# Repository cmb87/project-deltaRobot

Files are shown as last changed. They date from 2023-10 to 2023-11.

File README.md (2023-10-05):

# Nema17 Delta Robot (WIP!)

Parametric Delta Robot with NEMA17 stepper motors. By selecting the length of the profiles (e,f,rf,re) the desired workspace and characteristics can be achieved.

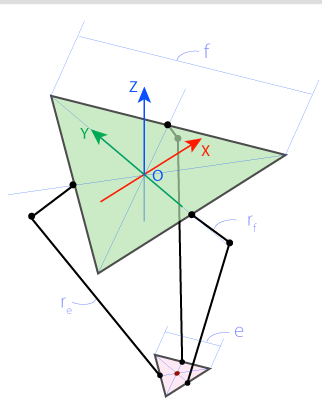
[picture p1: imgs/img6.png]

*Geometric parameters, sketch taken from https://hypertriangle.com/~alex/delta-robot-tutorial/*

# Software

For forward and inverse kinematics please check this awesome source: https://hypertriangle.com/~alex/delta-robot-tutorial/

# Construction

See https://www.thingiverse.com/thing:6248772

Pulley is a remix from here: https://www.thingiverse.com/thing:16627

## Electronics

CNC Shield: https://github.com/Protoneer/Fritzing_Parts

## To buy

    6x Senkkopfschrauben Edelstahl A2 V2A DIN 7991 Innensechskant M8 8 x 40 mm
    12x Gelenkkopf Außen M8  Uniballgelenk Kugelkopf Links und Rechts
    3x 6mm GT2 Zahnrad Pulley Ritzel Scheibe 40Zahn Ø8mm
    3x Nema17 Planetengetriebe Gear Reducer Ratio 5:1 φ5mm Input Shaft
    3x GT2 6mm geschloßener Zahnriemen 256
    6x Kugellager 61906 2RS Kugellager 6906 2RS 30x47x9mm
    3x M8 Gewindestange 10cm
    6x M8 Mutter
    3x Aluprofile (L5,) 20x20mm

    6x Aluprofile (L1 == f) 20x20mm
    3x Aluprofile (L2 == rf) 20x20mm
    3x Aluporfile (L3 == e) 10x10mm
    6x GFK/Aluminium Rundrohr 10cm  (L4==re) Durchmesser

    1x CNC Shield V3 Development Board for A4988 drivers Stepper for 3D printer compatible with Arduino
    1x Arduino Mega
    3x Micro Limit Switch
    3x Nema17 Stepper Motor

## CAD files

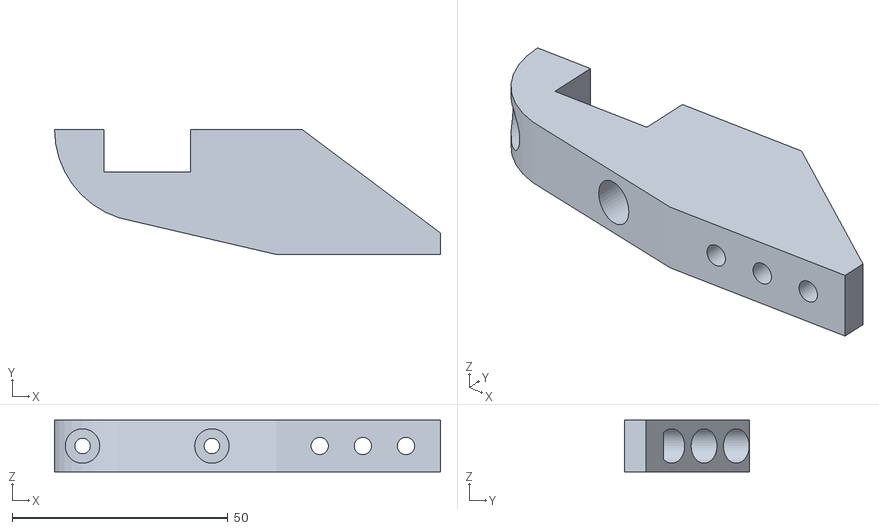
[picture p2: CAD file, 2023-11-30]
construction/3dprinted/plattformHolderUp.stl
89.5 x 29.0 x 12.0

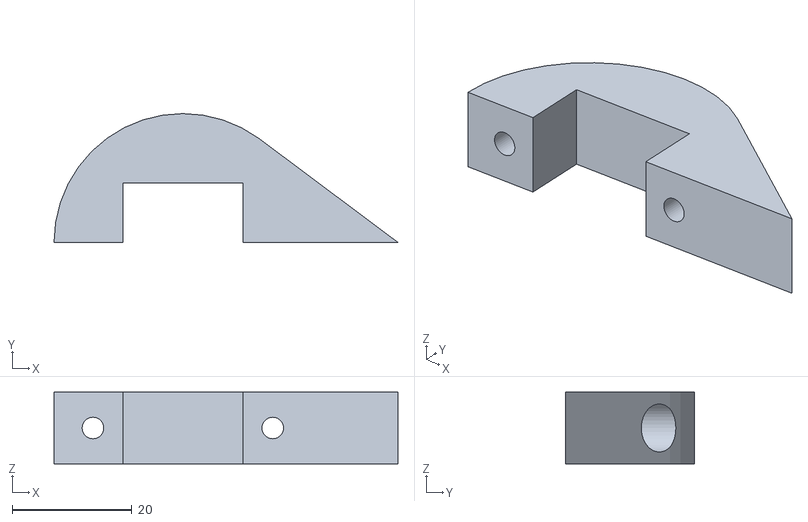
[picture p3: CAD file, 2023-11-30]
construction/3dprinted/plattformHolderLow.stl
57.4 x 21.5 x 12.0

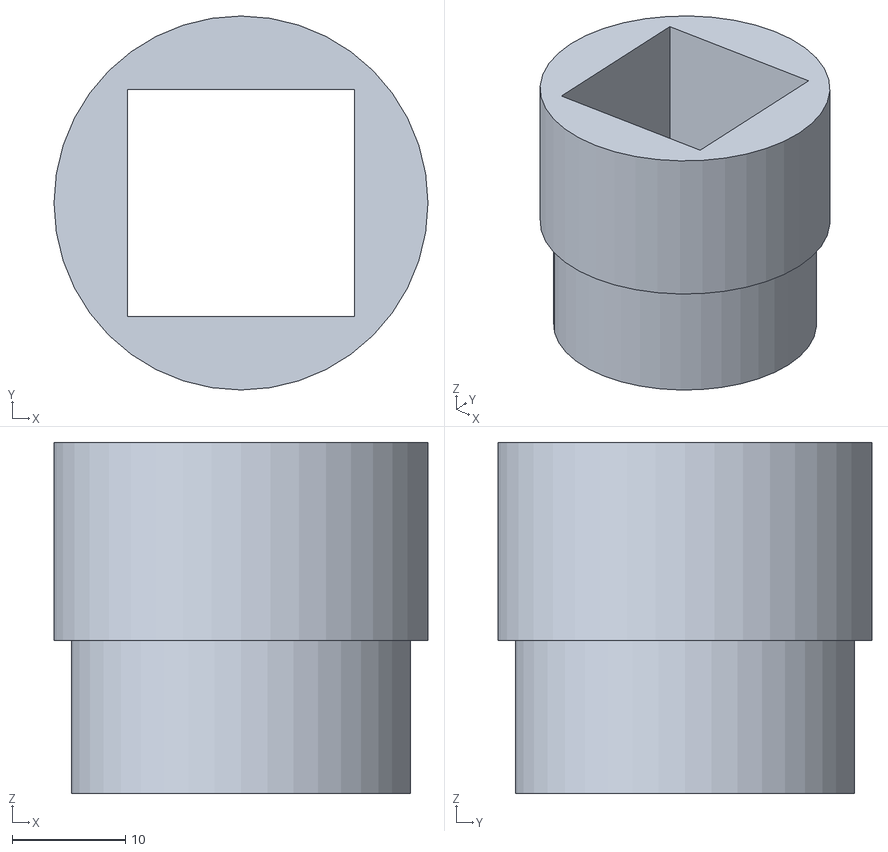
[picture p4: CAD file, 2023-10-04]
construction/3dprinted/attachment3.stl
33.0 x 33.0 x 31.0

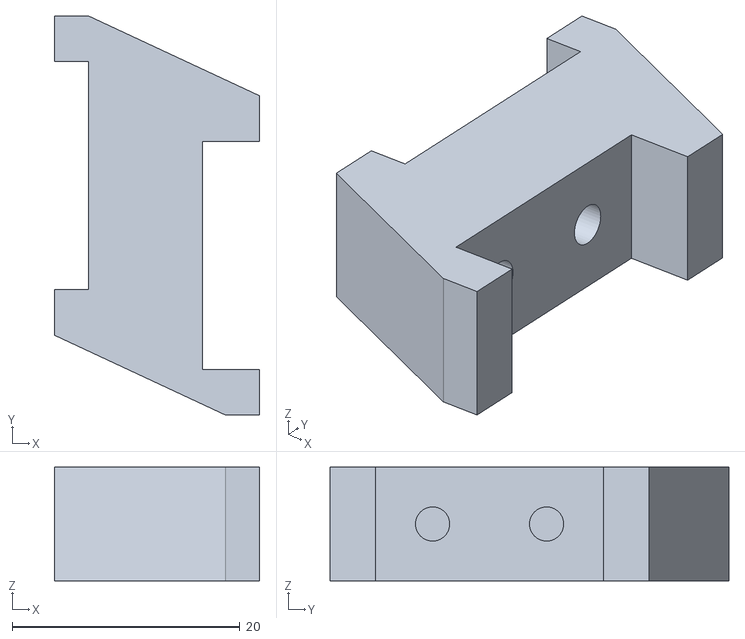
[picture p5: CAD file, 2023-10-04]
construction/3dprinted/arm_sensor_dist_v2.stl
18.0 x 35.0 x 10.0

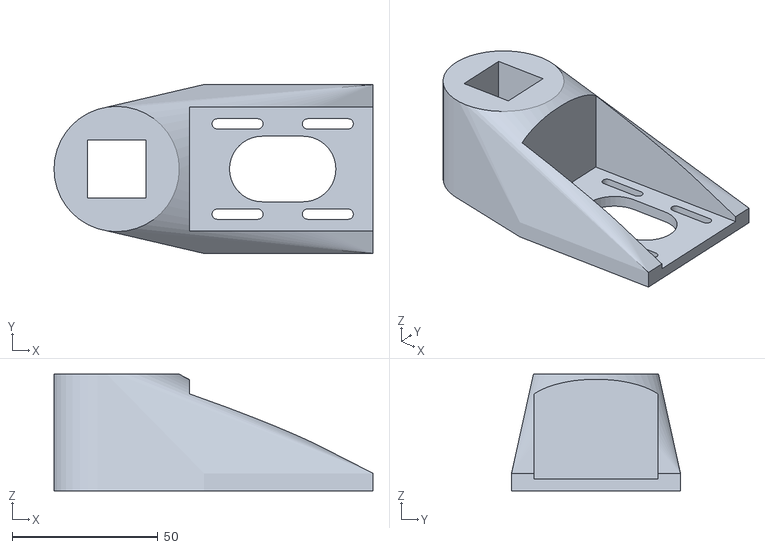
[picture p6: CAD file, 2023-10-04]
construction/3dprinted/motorHolder.stl
109.5 x 58.0 x 40.0

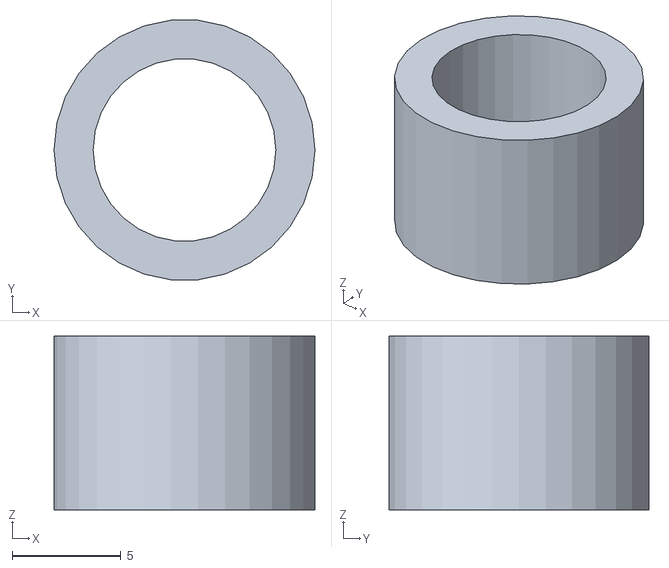
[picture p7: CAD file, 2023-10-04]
construction/3dprinted/distanceHullshort.stl
12.0 x 11.9 x 8.00

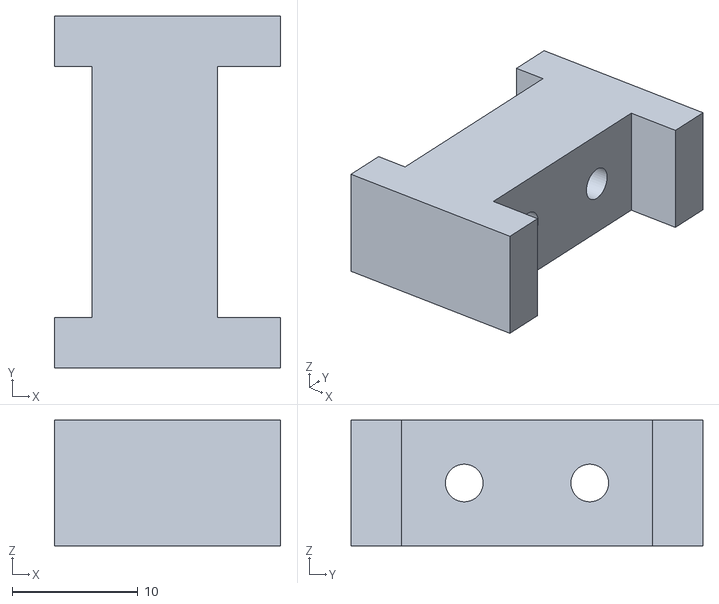
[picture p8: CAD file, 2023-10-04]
construction/3dprinted/arm_sensor_dist.stl
18.0 x 28.0 x 10.0

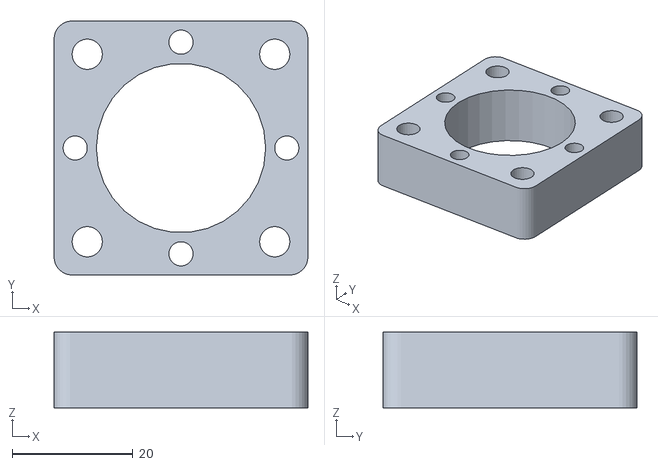
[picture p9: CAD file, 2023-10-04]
construction/3dprinted/gearadapter.stl
42.0 x 42.0 x 12.5

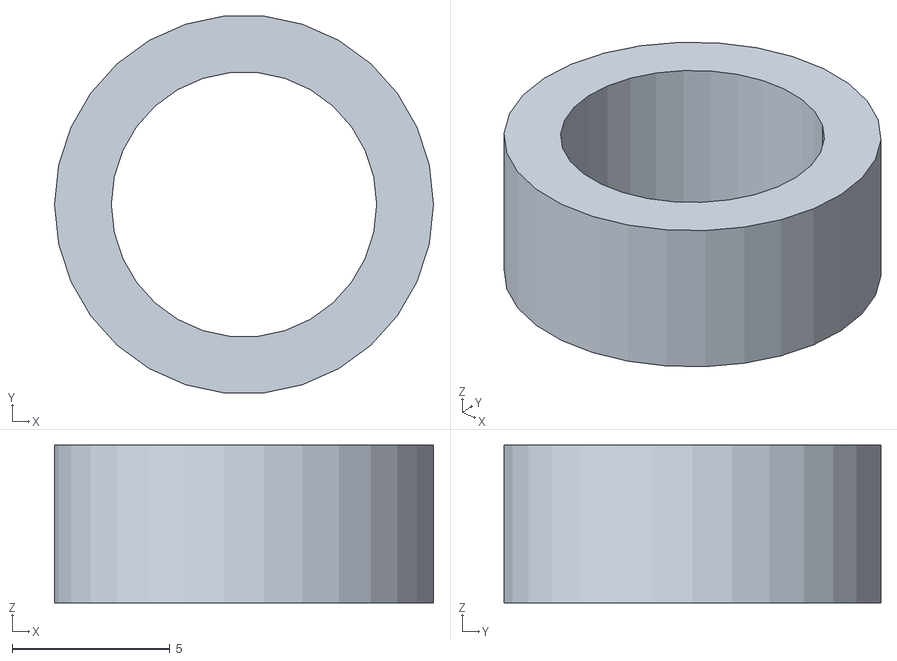
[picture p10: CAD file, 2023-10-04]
construction/3dprinted/distanceHullSupershort.stl
12.0 x 11.9 x 5.00

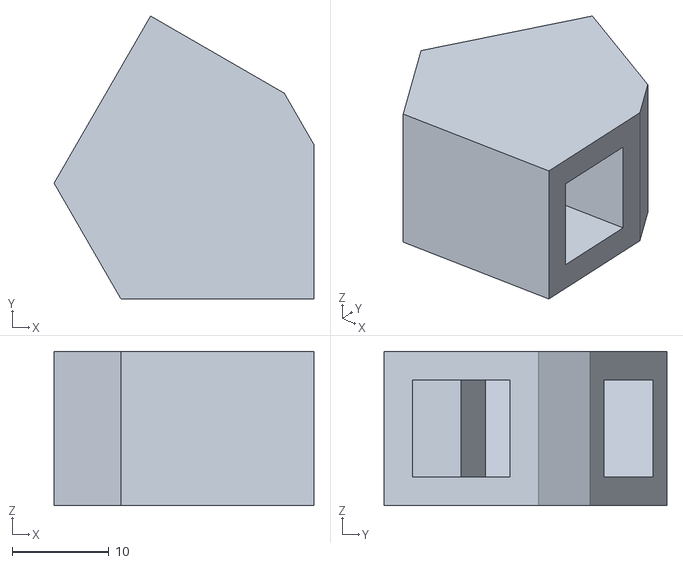
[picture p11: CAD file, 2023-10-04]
construction/3dprinted/lowerCorner.stl
26.9 x 29.3 x 16.0

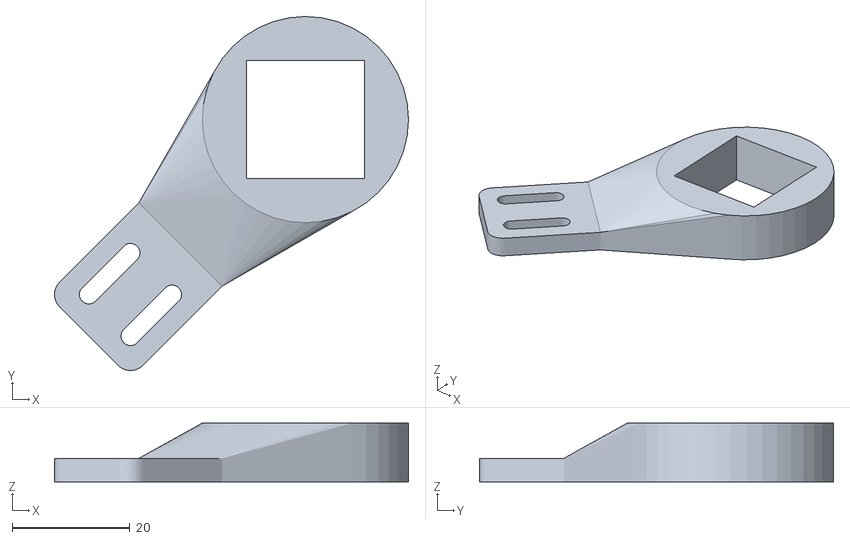
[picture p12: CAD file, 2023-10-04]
construction/3dprinted/arm_sensor_v2.stl
60.1 x 60.1 x 10.0

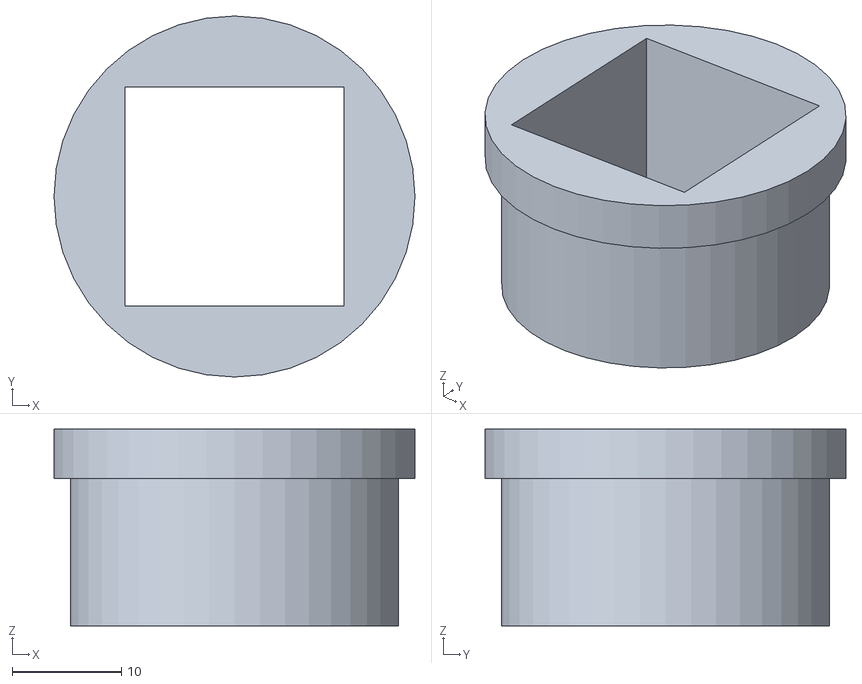
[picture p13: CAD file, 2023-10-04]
construction/3dprinted/attachment2.stl
33.0 x 33.0 x 18.0

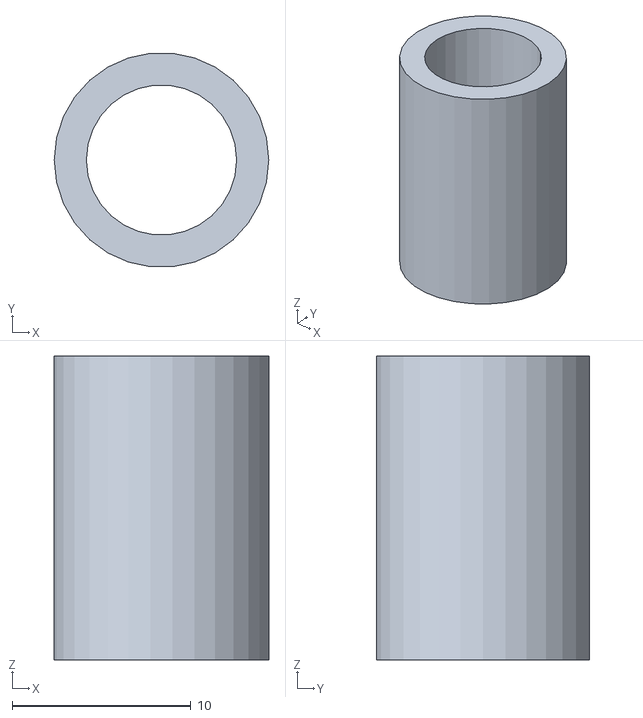
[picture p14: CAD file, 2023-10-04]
construction/3dprinted/distanceHull.stl
12.0 x 11.9 x 17.0

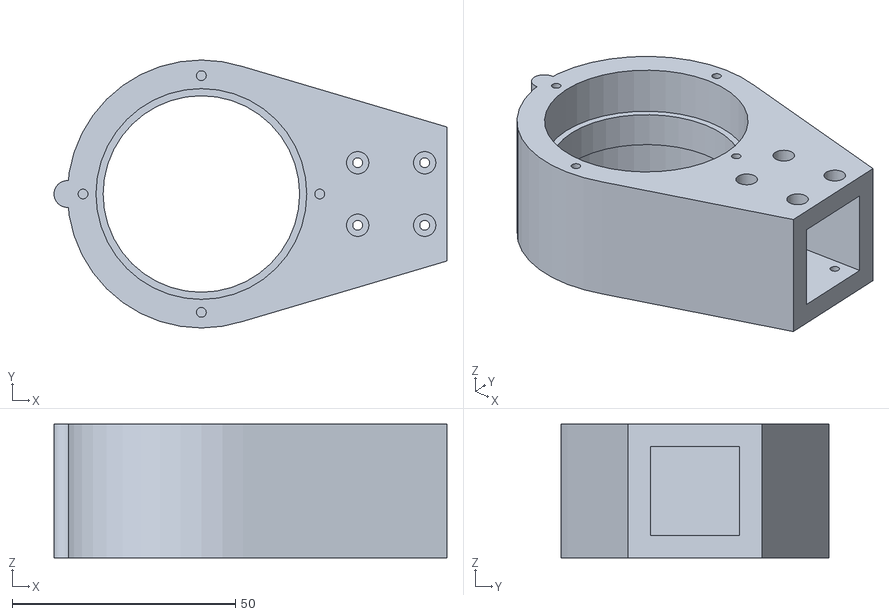
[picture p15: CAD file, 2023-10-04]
construction/3dprinted/arm.stl
88.0 x 60.0 x 30.0

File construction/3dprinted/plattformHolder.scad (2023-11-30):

//translate([50,0,+20])rotate([0,180,0])color("red")import("motor_nema17.stl");

difference(){
hull(){
translate([0,0,0])cylinder(r=43/2, h=12, $fn=40);
translate([30,-58/2,0])cube([38,5,12]);
}
translate([-20.0/2,-19.8/2,-1])cube([20.0,19.8,72]);  

translate([50,+70/2,6])rotate([90,0,0])cylinder(r=2, h=70, $fn=40);
translate([60,+70/2,6])rotate([90,0,0])cylinder(r=2, h=70, $fn=40);
translate([40,+70/2,6])rotate([90,0,0])cylinder(r=2, h=70, $fn=40);

translate([50,+70/2+15,6])rotate([90,0,0])cylinder(r=4, h=70, $fn=40);
translate([60,+70/2+15,6])rotate([90,0,0])cylinder(r=4, h=70, $fn=40);
translate([40,+70/2+15,6])rotate([90,0,0])cylinder(r=4, h=70, $fn=40);

translate([15,+70/2,6])rotate([90,0,0])cylinder(r=1.8, h=70, $fn=40);
translate([-15,+70/2,6])rotate([90,0,0])cylinder(r=1.8, h=70, $fn=40);

translate([-15,-5,6])rotate([90,0,0])cylinder(r=4, h=70, $fn=40);
translate([-15,70+5,6])rotate([90,0,0])cylinder(r=4, h=70, $fn=40);

translate([15,-5,6])rotate([90,0,0])cylinder(r=4, h=70, $fn=40);
translate([15,70+5,6])rotate([90,0,0])cylinder(r=4, h=70, $fn=40);


//translate([-30,0,-2])cube([120,100,42]); // Comment for low
translate([-30,-100,-2])cube([120,100,42]); // Comment for up

}

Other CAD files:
construction/3dprinted/arm_tip.stl
construction/3dprinted/lowerJoint.stl
construction/3dprinted/connector.stl
construction/3dprinted/arm_pulley.stl
construction/3dprinted/arm.scad
construction/3dprinted/arm_pulley.scad
construction/3dprinted/arm_sensor.scad
construction/3dprinted/arm_sensor_dist.scad
construction/3dprinted/arm_tip.scad
construction/3dprinted/arm_uppley.scad
construction/3dprinted/attachment2.scad
construction/3dprinted/attachment3.scad
construction/3dprinted/connector.scad
construction/3dprinted/corner.scad
construction/3dprinted/corner.stl
construction/3dprinted/gearadapter.scad
construction/3dprinted/lowerCorner.scad
construction/3dprinted/lowerJoint.scad
construction/3dprinted/motorHolder.scad

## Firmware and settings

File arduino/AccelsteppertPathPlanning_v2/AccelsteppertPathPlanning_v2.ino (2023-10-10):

#include <AccelStepper.h>
#include <MultiStepper.h>
#include "SerialTransfer.h"
#include "DeltaKinematics.h"


// Pin Definitions
#define stepPinX 2 //X.STEP
#define dirPinX 5 // X.DIR

#define stepPinY 3 //Y.STEP
#define dirPinY 6 // Y.DIR

#define stepPinZ 4 //Z.STEP
#define dirPinZ 7 // Z.DIR
  
#define enablePin 8


// On the CNC shield the limit switches are expected to be normally open and 
// are wired to ground with the internal pullup enabled. The switch will read high 
// when not actuated (open) and low when actuated (closed).
// Both switches for each axis go to one pin. X+ and X- go to pin 9, Y+ and Y- to 10, Z+ and Z- to 11.
#define limitPinX 9 
#define limitPinY 10
#define limitPinZ 11


// Delta Definitions
#define Multiplier 6.583333333333333 //2370.0/360  = 95.0/40.0 * 5.0/1.0 * 200/360 = 11.875 * 200/360 
#define HomeAngle 40 //11 degrees from vertical or 79 degrees from horizontal
#define Speed 2000
#define Acceleration 3000.0


// Create MultiStepper instance
AccelStepper Xaxis(1, stepPinX, dirPinX); // pin 2 = step, pin 5 = direction
AccelStepper Yaxis(1, stepPinY, dirPinY); // pin 2 = step, pin 5 = direction
AccelStepper Zaxis(1, stepPinZ, dirPinZ); // pin 2 = step, pin 5 = direction
DeltaKinematics DK(0.18,0.384,0.04,0.15);

MultiStepper steppers;  

// For serial transfer
SerialTransfer myTransfer;

struct __attribute__((packed)) CONTROLL {
  long theta1;
  long theta2;
  long theta3;
  long enabled;
  long home;
} controllStruct;

struct __attribute__((packed)) STATE {
  float theta1;
  float theta2;
  float theta3;
  long enabled;
  long home;
  long status;
} stateStruct;

struct __attribute__((packed)) POSITION {
  float x;
  float y;
  float z;
} positionStruct;


float P0[3] = {0, 0, 0};      // Initial positions  
float Pf[3] = {0, 0, 0};      // Final positions  
float V0[3] = {0, 0, 0};      // Initial velocities  
float Vf[3] = {0, 0, 0};      // Final velocities  
float T = 0.5;              // Total time (seconds)  
float dt = 0.0005;          // Time step (seconds)  


// ==================================
float cubicPath(float t, float P0, float Pf, float V0, float Vf, float T) {  
  float a0 = P0;  
  float a1 = V0;  
  float a2 = (3 * (Pf - P0) - (2 * V0 + Vf) * T) / (T * T);  
  float a3 = (2 * (P0 - Pf) + (V0 + Vf) * T) / (T * T * T);  
  
  float position = a0 + a1 * t + a2 * t * t + a3 * t * t * t;  
  return position;  
} 

// ==================================
void Enabled(){ digitalWrite(enablePin,LOW);}

// ==================================
void Disabled(){digitalWrite(enablePin,HIGH);}

// ==================================
void sendController(float theta1, float theta2, float theta3, long home, long status){
  /**
  Function which sends state back to controller (python script) via serial protocol.
  */

  stateStruct.theta1 = theta1;
  stateStruct.theta2 = theta2;
  stateStruct.theta3 = theta3;

  stateStruct.enabled = 1;
  stateStruct.home = home;
  stateStruct.status = status;

  uint16_t sendSize = 0;
  sendSize = myTransfer.txObj(stateStruct, sendSize);
  myTransfer.sendData(sendSize);

}

// ==================================
void homeMachine(){
  /**
  Function for homing machine
  */

  // Let controller know we are homing, all since we are not homed yet (=0), all angles are unkown (-1) and busy (503)
  sendController(-1, -1, -1, 0, 503);

  // Set speed for homing
  Xaxis.setSpeed(300); 
  Yaxis.setSpeed(300); 
  Zaxis.setSpeed(300); 

  // Important assumption: all arms are lower than HomeAngle!!!! Otherwise we crash :X
  while(digitalRead(limitPinX) == HIGH || digitalRead(limitPinY) == HIGH || digitalRead(limitPinZ) == HIGH)
  {
    if(digitalRead(limitPinX) == HIGH){
      Xaxis.runSpeed();
    } else {
      Xaxis.stop();
    }
    if(digitalRead(limitPinY) == HIGH){
      Yaxis.runSpeed();
    } else {
      Yaxis.stop();
    }
    if(digitalRead(limitPinZ) == HIGH){
      Zaxis.runSpeed();
    } else {
      Zaxis.stop();
    }  
  }
  
  // Store current steps
  Xaxis.setCurrentPosition((90-HomeAngle)*Multiplier);
  Yaxis.setCurrentPosition((90-HomeAngle)*Multiplier);
  Zaxis.setCurrentPosition((90-HomeAngle)*Multiplier);

  // Let controller know we are homed and ready for receiving orders
  sendController(
    90-HomeAngle*Multiplier,
    90-HomeAngle*Multiplier,
    90-HomeAngle*Multiplier,
    1,
    200
  );

}

// ==================================
void SetMotors(){  
  Serial.print("Error"); 
  Serial.println(DK.inverse()); // cal inverse Delta Kinematics
  double A = DK.a*Multiplier;
  double B = DK.b*Multiplier;
  double C = DK.c*Multiplier;
  Serial.println(DK.a);
  Serial.println(DK.b);
  Serial.println(DK.c);
  Serial.println(DK.x);
  Serial.println(DK.y);
  Serial.println(DK.z);
  Serial.println();
  Xaxis.moveTo(A);
  Yaxis.moveTo(B);
  Zaxis.moveTo(C);
  
  while(Xaxis.distanceToGo() != 0 || Yaxis.distanceToGo() != 0 || Zaxis.distanceToGo() != 0)
  {
    Xaxis.run();
    Yaxis.run();
    Zaxis.run();
  }
}

// ==================================
void setup(){

    Serial.begin(115200);
    myTransfer.begin(Serial);

    pinMode(limitPinX, INPUT_PULLUP);
    pinMode(limitPinY, INPUT_PULLUP);
    pinMode(limitPinZ, INPUT_PULLUP);

    pinMode(enablePin, OUTPUT);
    digitalWrite(enablePin,HIGH);

    Xaxis.setMaxSpeed(Speed);
    Xaxis.setSpeed(Speed);
    Xaxis.setCurrentPosition(0);
    Xaxis.setAcceleration(Acceleration);

    Yaxis.setMaxSpeed(Speed);
    Yaxis.setSpeed(Speed);
    Yaxis.setCurrentPosition(0);
    Yaxis.setAcceleration(Acceleration);

    Zaxis.setMaxSpeed(Speed);
    Zaxis.setSpeed(Speed);
    Zaxis.setCurrentPosition(0);
    Zaxis.setAcceleration(Acceleration);

    steppers.addStepper(Xaxis);
    steppers.addStepper(Yaxis);  
    steppers.addStepper(Zaxis);  

    // Home Robot
    Enabled();
    delay(1000); 
    homeMachine();
    delay(1000); 
  

}

// ==================================
void loop(){

  // ------------------------------------
  // Commands available on Serial ....
  if(myTransfer.available()){

    // Receive Serial 
    uint16_t recSize = 0;
    recSize = myTransfer.rxObj(controllStruct, recSize);

    // Home machine (if controll struct says so)
    if ( controllStruct.home ) {
      Disabled();
      delay(1000);
      Enabled();
      homeMachine();
    }

    // Tell controller latest position and that we are busy ...
    sendController(
      90-Xaxis.currentPosition()/Multiplier,
      90-Yaxis.currentPosition()/Multiplier,
      90-Zaxis.currentPosition()/Multiplier,
      1,
      503
    );

    // Motion Planning and Execution
    // Execute motion (move() = relative, moveTo() absolute)
    Xaxis.moveTo((90-controllStruct.theta1)*Multiplier);
    Yaxis.moveTo((90-controllStruct.theta2)*Multiplier);
    Zaxis.moveTo((90-controllStruct.theta3)*Multiplier);


    // Execute motion
    while(Xaxis.distanceToGo() != 0 || Yaxis.distanceToGo() != 0 || Zaxis.distanceToGo() != 0){
      Xaxis.run();
      Yaxis.run();
      Zaxis.run();
    }
  }

  // Tell controller latest position and that we are ready to receive new points ...
  sendController(
      90-Xaxis.currentPosition()/Multiplier,
      90-Yaxis.currentPosition()/Multiplier,
      90-Zaxis.currentPosition()/Multiplier,
    1,
    200
  );
  delay(100);

} 

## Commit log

2023-10-05 restructed construction
    [arm.scad, arm.stl, arm_pulley.scad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]
2023-10-10 fixed kinematic
2023-11-30 added holder2
    [plattformHolder.scad, plattformHolderLow.stl, plattformHolderUp.stl]
